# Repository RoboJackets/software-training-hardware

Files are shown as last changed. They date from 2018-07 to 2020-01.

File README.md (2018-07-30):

# software-training-hardware
Repository to contain all eagle files and any other electrical or mechanical files for the software training platform.

# Pin Mapping

| Pin | Type  In Actual | Type out actual | Notes |
|-|-|-|-|
| A0 | digital | PWM | |
| A1 | digital | PWM | |
| A2 | analog  | Na | |
| A3 | analog  | Na | |
| A4 | analog  | Na | |
| A5 | digital | PWM | |
| 13 | digital  | PWM | |
| 12 | Na  | Na | do not use |
| 27 | digital  | PWM | |
| 33 | analog | PWM | |
| 15 | digital  | PWM | |
| 32 | analog | PWM | |
| 14 | digital  | PWM | |

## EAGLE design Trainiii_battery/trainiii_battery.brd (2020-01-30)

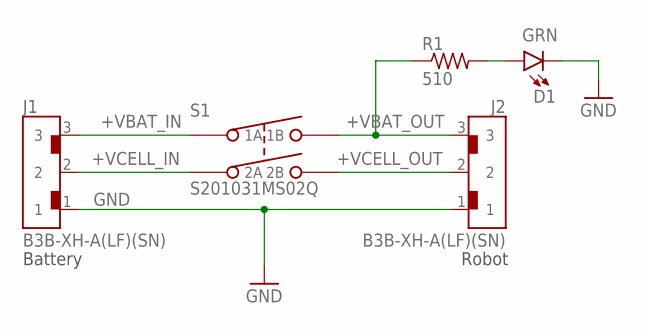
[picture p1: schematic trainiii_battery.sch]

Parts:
D1: GRN; LED-0603
J1, J2: B3B-XH-A(LF)(SN)
R1: 510; R0603
S1: S201031MS02Q; S201

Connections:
+VBAT_IN: J1.3, S1.1 (1A)
+VBAT_OUT: J2.3, R1.1, S1.2 (1B)
+VCELL_IN: J1.2, S1.4 (2A)
+VCELL_OUT: J2.2, S1.5 (2B)
GND: D1.C, J1.1, J2.1
LED_IN: D1.A, R1.2

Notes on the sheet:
Battery
Robot

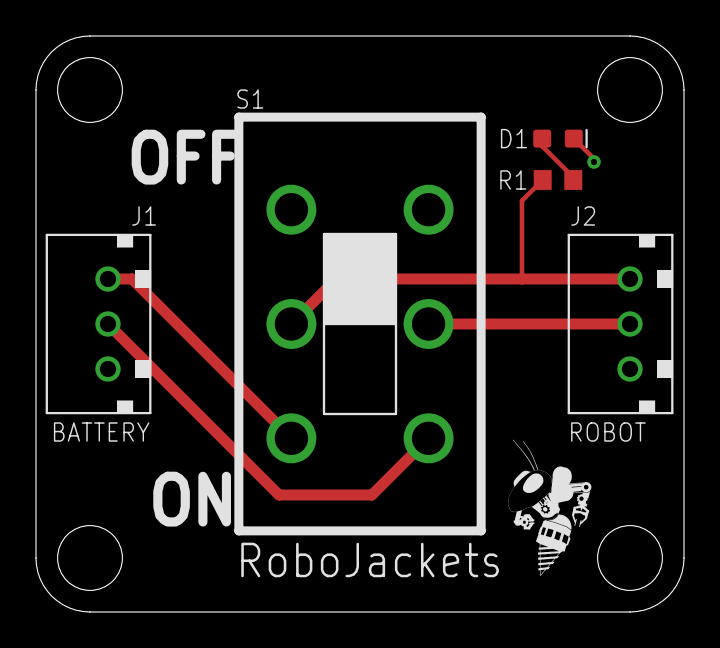
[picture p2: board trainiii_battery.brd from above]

Board: 2 copper layers, 36.0 x 32.0 mm, 6 parts (0 on the bottom side), 6 nets.

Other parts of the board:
U$2: ROBOBUZZ_0.4X

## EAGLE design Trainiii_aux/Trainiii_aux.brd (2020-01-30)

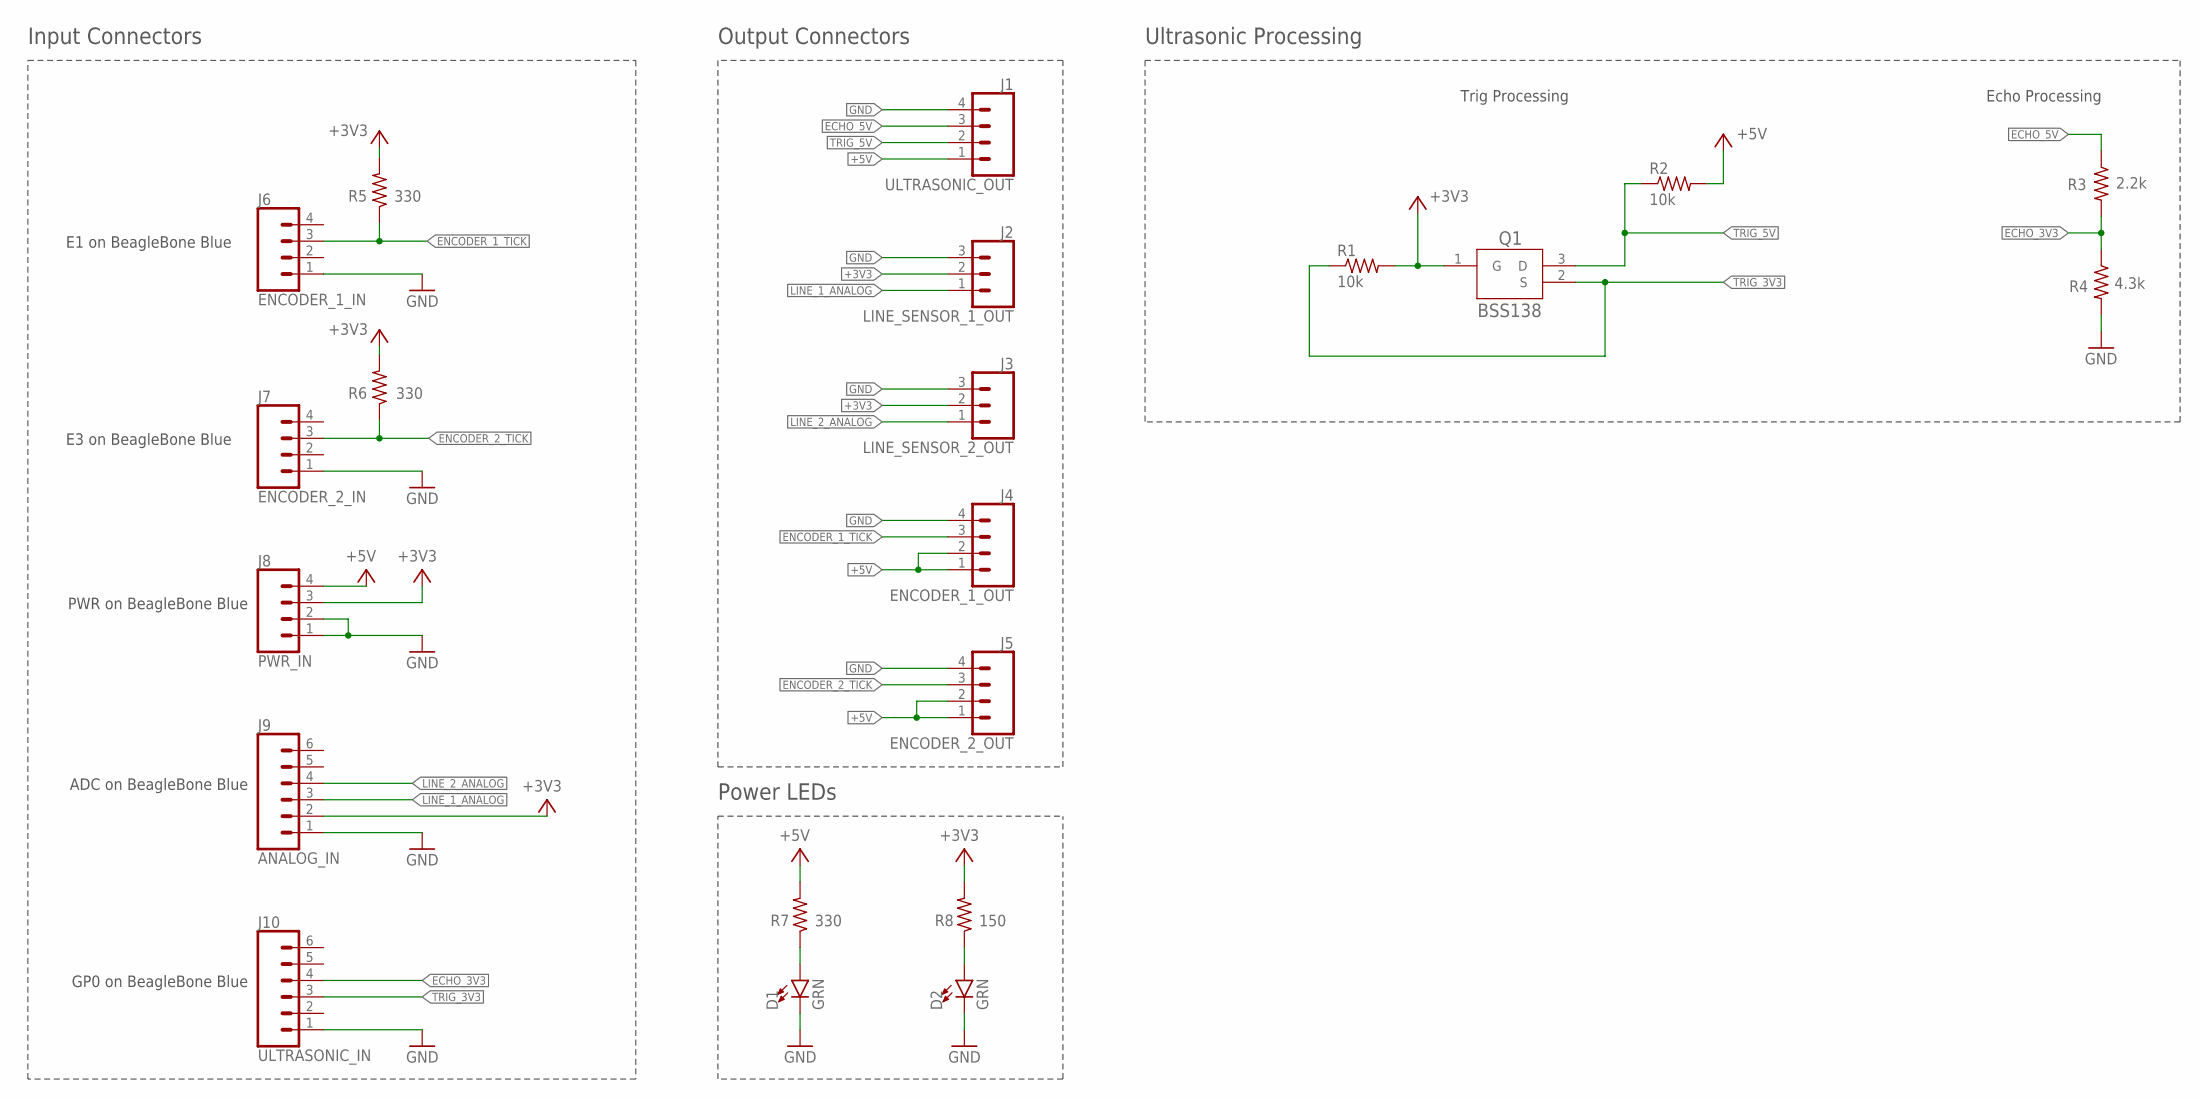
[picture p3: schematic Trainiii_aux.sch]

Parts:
D1, D2: GRN; LED-0603
J1: ULTRASONIC_OUT; 1X04
J2: LINE_SENSOR_1_OUT; 1X03
J3: LINE_SENSOR_2_OUT; 1X03
J4: ENCODER_1_OUT; 1X04
J5: ENCODER_2_OUT; 1X04
J6: ENCODER_1_IN; 1X04
J7: ENCODER_2_IN; 1X04
J8: PWR_IN; 1X04
J9: ANALOG_IN; 1X06
J10: ULTRASONIC_IN; 1X06
Q1: BSS138; SOT-23-3L
R1, R2: 10k; R0603
R3: 2.2k; R0603
R4: 4.3k; R0603
R5, R6, R7: 330; R0603
R8: 150; R0603

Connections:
3V3_LED: D2.A, R8.1
5V_LED: D1.A, R7.1
+3V3: J2.2, J3.2, J8.3, J9.2, Q1.1 (G), R1.2, R5.2, R6.2, R8.2
+5V: J1.1, J4.1, J4.2, J5.1, J5.2, J8.4, R2.2, R7.2
ECHO_3V3: J10.4, R3.2, R4.1
ECHO_5V: J1.3, R3.1
ENCODER_1_TICK: J4.3, J6.3, R5.1
ENCODER_2_TICK: J5.3, J7.3, R6.1
GND: D1.C, D2.C, J1.4, J2.3, J3.3, J4.4, J5.4, J6.1, J7.1, J8.1, J8.2, J9.1, J10.1, R4.2
LINE_1_ANALOG: J2.1, J9.3
LINE_2_ANALOG: J3.1, J9.4
TRIG_3V3: J10.3, Q1.2 (S), R1.1
TRIG_5V: J1.2, Q1.3 (D), R2.1

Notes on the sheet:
Output Connectors
Ultrasonic Processing
Trig Processing
Echo Processing
E1 on BeagleBone Blue
E3 on BeagleBone Blue
PWR on BeagleBone Blue
ADC on BeagleBone Blue
GP0 on BeagleBone Blue
Input Connectors
Power LEDs

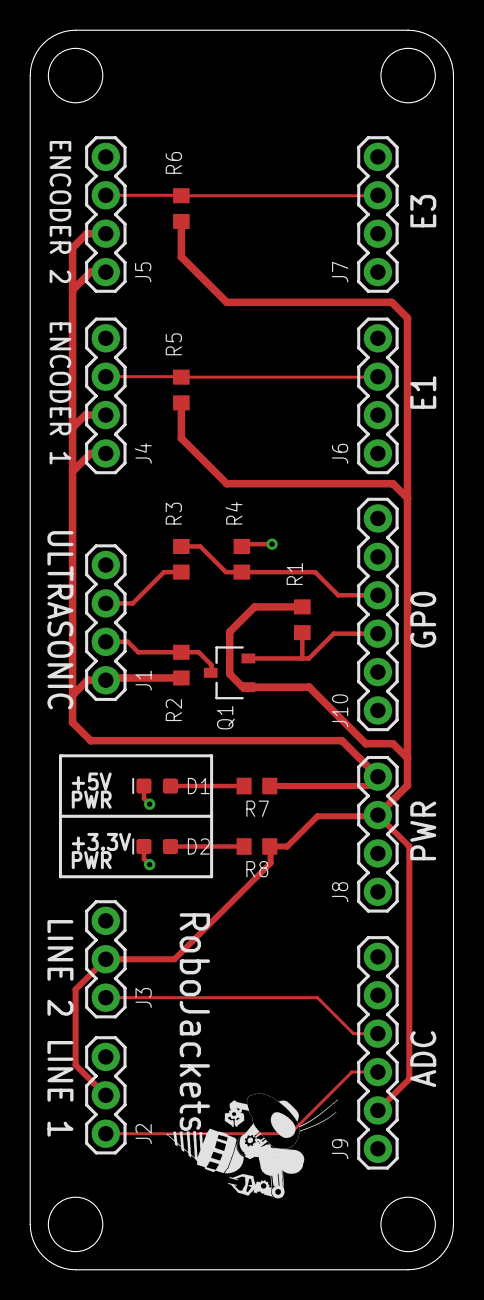
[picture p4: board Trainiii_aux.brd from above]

Board: 2 copper layers, 28.0 x 82.0 mm, 22 parts (0 on the bottom side), 13 nets.

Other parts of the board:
U$1: ROBOBUZZ_0.6X

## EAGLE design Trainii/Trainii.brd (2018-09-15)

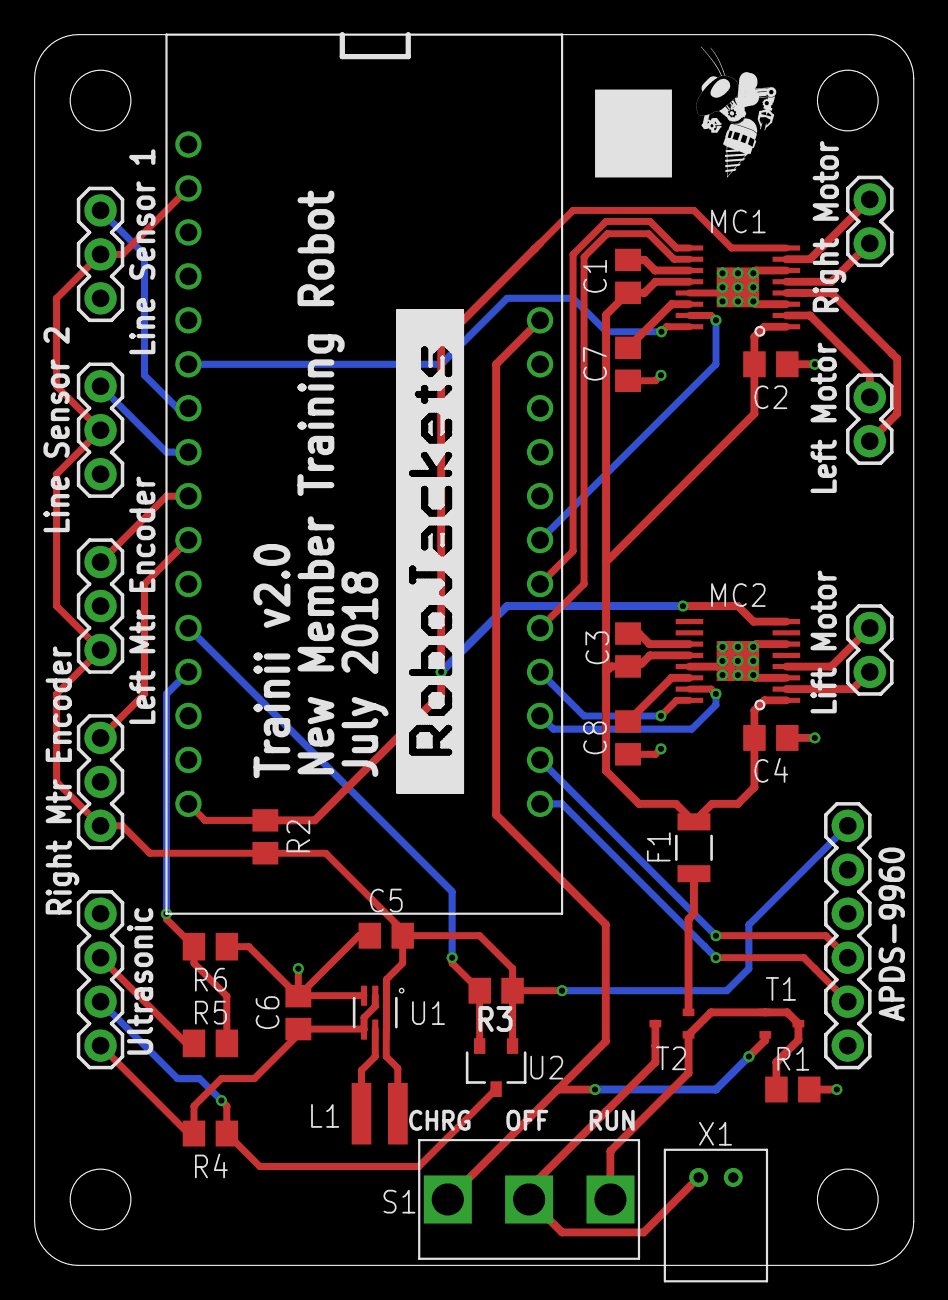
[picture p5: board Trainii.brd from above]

Board: 2 copper layers, 50.8 x 71.1 mm, 36 parts (0 on the bottom side), 36 nets.

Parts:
C1, C3: 0.01uF; C0805
C2, C4: 10uF; C0805
C5, C6: 10uF 16V; C0805
C7, C8: 2.2uF; C0805
F1: 0ZCJ0100FF2E; 1206
J1: APDS-9960; 1X06
J2: Left Mtr Encoder; 1X03
J3: Right Mtr Encoder; 1X03
J4: Line Sensor 1; 1X03
J5: Line Sensor 2; 1X03
J6: Ultrasonic; 1X04
J7: Left Motor; 1X02
J8: Right Motor; 1X02
J9: Lift Motor; 1X02
L1: 4.7uH; VLS3012HBX
M1: ESP32
MC1, MC2: DRV8833; HTSSOP-16
R1, R2, R3, R4: 10kΩ; R0805
R5: 2k2Ω; M0805
R6: 4k3Ω; M0805
S1: 100SP3T
T1, T2: MCH3383SC-70FL; SOTFL65P210X90-3
U1: TPS61222DCKR; DCK6
U2: BSS138; SOT-23-3L
U$2: ROBOJACKETS
U$6: ROBOBUZZ_0.4X
X1: JST-PH2; JST-PH

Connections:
3V3: C5.1, J1.6, J2.1, J3.1, J4.2, J5.2, L1.1, M1.3V, R2.2, R3.1, U1.1, U1.6, U2.1
+5V: C6.1, J6.1, R4.1, U1.2, U1.4
ECHO_3V3: M1.MI, R5.2, R6.1
ECHO_5V: J6.3, R5.1
GND: C2.2, C4.2, C5.2, C6.2, C7.2, C8.2, J1.4, J2.2, J3.2, J4.1, J5.1, J6.4, M1.GND, MC1.3, MC1.6, MC1.13, MC1.17, MC2.3, MC2.6, MC2.13, MC2.17, R1.1, R6.2, U1.3, X1.1
LEFT_0: J7.1, MC1.2
LEFT_1: J7.2, MC1.4
LEFT_A: M1.A1, MC1.16
LEFT_B: M1.A10, MC1.15
LIFT_0: J9.1, MC2.2
LIFT_1: J9.2, MC2.4
LIFT_A: M1.A7, MC2.16
LIFT_B: M1.A6, MC2.15
LINE_OUT_1: J4.3, M1.A2
LINE_OUT_2: J5.3, M1.A3
MOTOR_FAULT: M1.21, MC1.8, MC2.8, R2.1
unnamed: L1.2, U1.5
unnamed: R1.2, S1.3, T1.1, T1.3, T2.1
unnamed: C8.1, MC2.14
unnamed: C1.1, MC1.11
unnamed: C7.1, MC1.14
unnamed: C3.1, MC2.11
RIGHT_0: J8.1, MC1.7
RIGHT_1: J8.2, MC1.5
RIGHT_A: M1.A9, MC1.9
RIGHT_B: M1.A8, MC1.10
SCL: J1.3, M1.22
SDA: J1.2, M1.23
TICK_LEFT: J2.3, M1.A4
TICK_RIGHT: J3.3, M1.A5
TRIG_3V3: M1.MO, R3.2, U2.2
TRIG_5V: J6.2, R4.2, U2.3
VBAT: S1.2, T2.3, X1.2
VBAT_HUZZAH: M1.BAT, S1.1, T1.2
VBAT_MOTOR: F1.1, T2.2
VBAT_MOTOR_FUSE: C1.2, C2.1, C3.2, C4.1, F1.2, MC1.1, MC1.12, MC2.1, MC2.12

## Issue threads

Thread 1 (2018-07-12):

Add separate charging port and state switch

jspall0327, 2018-07-12:
Add a JST PH female port with a 3-pos switch that either isolates the battery, connects the battery to the HUZZAH and motors, or just connect the battery to the HUZZAH

Closed 2018-08-01.

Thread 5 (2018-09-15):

Flip charge and run label on board

jspall0327, 2018-09-15:

Closed 2020-01-30.

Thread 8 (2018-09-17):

Correct FET issues

jspall0327, 2018-09-17:
Rotate T1, make normally closed, increase package size, remove T2

Closed 2020-01-30.

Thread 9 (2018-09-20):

Drive motor enable pin from digital output

jspall0327, 2018-09-20:

barulicm, 2018-09-20:
If the current problem is uncontrollable / random uController outputs while it loads the firmware, would this actually fix it?

jspall0327, 2018-09-20:
It might. Not really sure. But we should probably stop motors on disconnect and stuff anyway.

JasonGibson274, 2018-09-20:
We already stop motors on disconnect from the firmware. We might want to check if there is an open pin that does not randomly do this first. If all pins behave the same then there might be nothing we can do.

Closed 2020-01-30.

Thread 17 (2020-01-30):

Remove VDD connection to ADC pin

jspall0327, 2020-01-30:
ADC pin outputs 1.8V as analog reference. VDD connected assuming setting analog reference (wrong)

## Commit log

2018-05-16 corrected issues in library and start creating the schematic
    [Tranii.brd, Tranii.sch]
2018-05-16 finished pin mapping
    [Tranii.brd, Tranii.sch]
2018-05-17 cleaned up schematic
    [Tranii.brd, Tranii.sch]
2018-05-18 finished schematic
    [Tranii.brd, Tranii.sch]
2018-05-18 renamed files to fix typo
    [Trainii.brd, Trainii.sch]
2018-05-18 Changed a few parts, corrected small wiring connections, routed board
    [Trainii.brd, Trainii.sch]
2018-05-18 Ran design rule checks
    [Trainii.brd]
2018-05-19 Squeezes board to 2in width.
    Re-layout to try to fit board into last draft of the mechanical CAD.
    [Trainii.brd]
2018-05-19 Fixes spacing between ECHO3.3 and R8
    [Trainii.brd]
2018-05-19 Fixes location of J9
    It was slightly off of the 0.1" grid I tried to fit all of the connectors to.
    [Trainii.brd]
2018-05-19 Fixes header spacing for the Huzzah ESP32 in Trainii.lbr
    [Trainii.brd, Trainii.sch]
2018-05-20 Realigned some routing to pads on ICs
    [Trainii.brd]
2018-05-25 Added fuse, changed power source, fixed some routing widths
    [Trainii.brd, Trainii.sch]
2018-05-28 Prepared gerber and BOM for order
    [Trainii BOM.csv, Trainii.brd]
2018-07-11 Updated Library, began fixing schematic
    [Trainii.brd, Trainii.sch]
2018-07-11 Continued library update and finished schematic driver correction
    [Trainii.brd, Trainii.sch]
2018-07-18 Added new battery connector
    [Trainii.brd, Trainii.sch]
2018-07-23 edited schematic to include 3-position switch to select charging, running, or off
    [Trainii.brd, Trainii.sch]
2018-07-26 Updated Libraries, corrected component placement
    [Trainii.brd, Trainii.sch]
2018-07-26 Initial component placement before routing
    [Trainii.brd, Trainii.sch]
2018-07-28 Initial routing
    [Trainii.brd, Trainii.sch]
2018-07-29 Finished routing, exported images
    [Trainii BOM.csv, Trainii.brd, Trainii.sch]
2018-07-29 Added Switch Labels
    [Trainii.brd]
2018-07-31 Design Review Changes
    [Trainii.brd, Trainii.sch]
2018-07-31 A E S T H E T I C S
    [Trainii.brd]
2018-07-31 Moved robobuzz
    [Trainii.brd]
2018-07-31 Added place for numbering, updated images and bom
    [Trainii BOM.csv, Trainii.brd]
2018-08-03 Increase resistance to reduce current
    [Trainii.brd, Trainii.sch]
2018-08-03 Adjusted small routes
    [Trainii.brd]
2018-08-07 Removed additional transistor to allow for charging to work correctly
    [Trainii.brd, Trainii.sch]
2018-08-07 Added gerbers
    [Trainii.brd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]
2018-08-07 Corrected gerber
    [copper_bottom.gbr, copper_top.gbr, drills.xln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]
2019-07-07 Initial commit of battery switch board
    [trainiii_battery.brd, trainiii_battery.sch]
2019-07-07 Added status LED, cleaned up board layout
    [trainiii_battery.brd, trainiii_battery.sch]
2019-07-10 Final Order v1.0
    [trainiii_battery.brd, trainiii_battery.sch]
2019-08-07 Initial Restructure and Trainiii Aux board design
    [Trainiii_aux.brd, Trainiii_aux.sch, trainiii_battery.brd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]
2019-08-07 Finish initial version of Aux board
    [Trainiii_aux.brd, Trainiii_aux.sch]
2019-08-07 Flipped location of RoboJackets, RoboBuzz
    [Trainiii_aux.brd]
2019-08-13 Created Trainiii Aux gerber
2020-01-30 Removed Traini v2 files
    [Trainii BOM.csv, Trainii.brd, Trainii.sch]

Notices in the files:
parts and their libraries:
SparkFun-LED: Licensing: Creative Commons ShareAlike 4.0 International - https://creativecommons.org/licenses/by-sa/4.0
